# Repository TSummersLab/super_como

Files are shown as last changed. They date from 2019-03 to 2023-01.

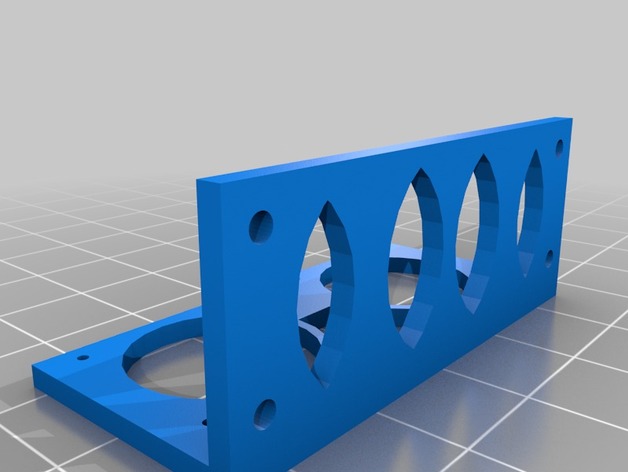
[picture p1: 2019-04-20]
CAD/ultrasonic_mount/images/f159fd88af9eb30a68ea307b06156ffa_preview_featured.jpg

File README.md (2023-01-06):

# Super COMO
Super COMO is an autonomous car platfrom at the University of Texas at Dallas. It is a hardware upgrade over the [COMO platform](https://github.com/TSummersLab/como).

Check out [our website](https://omarkabbas.github.io/supercomo/) for details about car assembly, build, and other guides and tutorials.

## Installation Guide

Before installing the Super COMO packages, perform a full JetPack installation on the Jetson TX2. For the package, JetPack 3.2.1 was installed. 

After installing JetPack, follow the steps below to setup Super COMO.

1. Configure repositories:
Configure repositories to allow "restricted," "universe," and "multiverse." Do this by following the instructions in [this link](https://help.ubuntu.com/community/Repositories/Ubuntu).

2. Clone super_como :
Clone the repository to your home directory. In a terminal window run:
```
cd ~ && git clone https://github.com/The-SS/super_como
```

3. Navigate to setup folder:
In terminal, navigate to the `setup` folder in `super_como` by running:
``` 
cd ~/super_como/setup
```

4. Configure git (if not configured):
Configure git either manually or by running `git_config_setup.sh`. You can run the setup file as follows:
```
./git_config_setup.sh
```

5. Run the following scripts:
```
./install_programs.sh

./install_ros.sh

```

6. Download and install the ZED SDK:
- Go to the [ZED downloads](https://www.stereolabs.com/developers/release/#sdkdownloads_anchor) website and download the [ZED SDK for Jetson TX2 with JetPack 3.2 and CUDA 9](https://download.stereolabs.com/zedsdk/2.7/tegrax2).

- Once it downloads, either used `chmod +x <file_name>` to make the file and executable or right click it --> permissions --> allow executing file as a program.

- Run the script by `cd` to file location in a terminal and typing `./` followed by the file name.

7. Setup the device rules:
Run the rules set up script:
```
sudo ./rules_setup.sh
```

This script will reload the rules, but we recommend restarting the machine to ensure that the rules are in effect.

8. Run the build script:
The `build.sh` script at the root of the super_como package builds the catkin workspace. In a terminal window, navigate to the root of the super_como package then run the following command:
```
cd ~/super_como
./build.sh
```

9. Generate the `ros_lib` libraries for arduino:
- Go the the Arduino `libraries` direcotry: 
```
cd ~/arduino-1.8.7/libraries
``` 
- Remove any previous `ros_lib` directory:
```
rm -fr ros_lib
```
- Generate the new libraries:
```
rosrun rosserial_arduino make_libraries.py .
```

For more details see the Install ros_lib into the Arduino Environment section [here](http://wiki.ros.org/rosserial_arduino/Tutorials/Arduino%20IDE%20Setup).

10. Source the workspace:
Every time a new terminal window is open you have to source your workspace.
```
source ~/super_como/workspace/devel/setup.bash
```
Alternatively, you can add the above to your bashrc file to avoid having to run it every time. To do that, run the following in a terminal.
```
echo "source ~/super_como/workspace/devel/setup.bash" >> ~/.bashrc
```
Once this runs you have to restart your terminal or source the bashrc file as follows:
```
source ~/.bashrc
```

11. Add the Lidar to ethernet networks:
- Open `Network Connections`.
- Click on `Add`.
- In the new window do the following:
	- Change the connection name to `lidar`
	- In the `General` tab, check the `Automatically connect to this network when it is available` and `All users may connect to this network` options
	- In the `IPv4 Settings` tab, change the `method` to `Manual` and add the following in `Addresses`:
		- address: 192.168.0.15
		- netmask: 255.255.255.0 (this will change to 24)
		- leave the `gateway` field empty
	- Click save.

12. Edit the USB port names:
The rules file generated by `rules_setup.sh` creates symbolic links for devices that should be used instead of the port names generated by Linux. The full list of symbolic links found in `/etc/udev/rules/99-device-rules.rules` is:
- `/dev/imu`: IMU
- `/dev/vesc`: VESC 
- `/dev/teensy`: Teensy
- `/dev/gps`: GPS module
- `/dev/elp/back`: back elp camera
- `/dev/elp/right`: righ elp camera
- `/dev/elp/left`: left elp camera
- `/dev/elp/front`: front elp camera

These links should be used in the package (instead of `/dev/ttyUSB*`, `/dev/ttyACM*`, or `/dev/video*`). Make the following modifications to the package:
- In `~/super_como/super_como/workspace/src/racecar/racecar/config/racecar-v2/vesc.yaml` change the `port` parameter under `vesc_driver` to `/dev/vesc`.
- In `~/super_como/workspace/src/razor_imu_9dof/config/razor.yaml` change the `port` parameter to `/dev/imu`.
- In `~/super_como/workspace/src/razor_imu_9dof/nodes/imu_node.py` change the `default_port` variable to `'/dev/imu'` (line 110). The updated line should be: `default_port='/dev/imu'`.

13. If running YOLO, change the `darknet_ros` camera topic: 
In `~/super_como/workspace/src/darknet_ros/darknet_ros/config/ros.yaml` change the `topic` parameter under `camera_reading` in `subscribers` to the desired image topic. For example that could be the `/zed/left/image_raw_color` topic if using the ZED or ZED mini cameras. Check the [YOLO github repository](https://github.com/leggedrobotics/darknet_ros/tree/7bc7ec0517b7107712da998f975584c88ed15f77) for more details.

## Operating the Package
Operating the package is a two step process:
1. Starting the sensors and hardware
2. Starting an autonomous feature
This decoupling allows for easy switching between autonomous features wihtout having to restart all sensor operation

#### To Start the Sensors and Hardware
1. Open `super_como/workspace/src/hardware_interface/launch/super_como.launch` and edit the `On/Off Switches` section (and save the changes). 
	- Setting the default value to `true` will start the component
	- Setting the default value to `false` will skip starting the component
2. Run the following in a terminal window:
```
roslaunch hardware_interface super_como.launch
```

The super_como.launch provides an all-in-one solution to starting all hardware components. Nonetheless, individual scripts can be launched. Any of the scripts in `super_como/workspace/src/hardware_interface/launch` or any of the other packages in workspace can be run individually to control a single (or multiple) device(s).

#### To Start an Autonomous Feature
1. Determine what application to run and edit the `super_como.launch` script to enable all the required sensors.
2. Run the appropriate launch file from `super_como/workspace/src/control/launch` to perform the desired feature by running the following in a terminal window: 
```
roslaunch control <file_name> 
```
Here, <file_name> is the desired launch file name.

Some of the autonomous features include the following:
- `hallway_navigation.launch`: requires the Hokuyo UST-10LX lidar
- `hallway_nav_wth_object_detection.launch`: requires the Hokuyo UST-10LX lidar and the camera used by `darknet_ros` (yolo) (ZED camear by default)
- `line_follower.launch`: requires the ZED camera
- `line_follower_with_lidar.launch`: requires the Hokuyo UST-10LX lidar and the ZED camera
- `darknet_ros.launch`: requires the camera used by `darknet_ros` (yolo) (ZED camear by default)

Other autonomous driving features can be designed similar to the first four included feature

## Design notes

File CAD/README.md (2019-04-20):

# CAD Files
CAD files for the Super COMO car.

# Description
- decks: 
	- Contains SolidWorks files (SLDPRT) for the decks and engineering drawings (PDF)
	- Machine the parts as follows:
		- Deck 1, Deck 2: Plastic
		- Deck 3: Aluminum
- elp_pole_mount:
	- Contains the stl files for the elp camera pole mount design (base and holder)
	- The original designer of these parts is Cheng Hao Yuan (chengyuan@berkeley.edu) and the parts are part of the [UCB BARC project](http://www.barc-project.com/) and can also be found [here](https://github.com/MPC-Berkeley/barc/tree/master/CAD/camera%20fixture)
	- 3D print the desired number using any material (ABS is fine)
- elp_seat_mount:
	- Contains the stl file for the elp camera seat mount design
	- The original designer of this part is Kevin Daniel (kmd140630@utdallas.edu)
	- 3D print the desired number using any material (ABS is fine)
- encoder_mount:
	- Contains the stl file and SolidWorks file (SLDPRT) for the encoder mount
 	- 3D print using any material (ABS is fine)
- encoder_disk:
	- Contains the stl file and SolidWorks file (SLDPRT) for the encoder disk
 	- 3D print using any material (ABS is fine)
- ultrasonic_mount:
	- Contains the stl file for the ultrasonic sensor mount (files/Ultraschallsensorhalterung_4.stl)
	- The original design is part of the Thingiverse database
	- 3D print using any material (ABS is fine)
- teensy_ckt:
	- Contains the Eagle board (BRD) and schematic (SCH) file, Gerber files, and PDFs
 for the teensy ckt
	- The schematic can be used to assemble the circuit. The Gerber files can be used to order the PCB.

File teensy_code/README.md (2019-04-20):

# Teensy Code

Contains the Teensy code to be flashed on the Teensy 3.5.

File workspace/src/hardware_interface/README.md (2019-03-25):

# SuperCOMO Hardware Interface

### Package Overview

This package is design to provide the necessary interface with the car's hardware. This includes initializing and starting the following devices:
- ZED camera
- Razor 9DoF IMU
- Hokuyo ust-10LX LIDAR
- VESC 

When this package establishes a communication with the hardware, it also provides ROS topics for other packages to publish/subscribe to the sensor/control hardware. These topics are documented below.

### Package Nodes

### Pakcage Topics

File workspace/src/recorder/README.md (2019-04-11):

### Recording the Basic Data 

This program record the basic out put of the main components including, Zed left and right images, LIDAR, IMU, and Teensy. It was created to reduce the data recorded as recording every message creates a huge file. 
#### Running Recorder

To run the program us rosrun to run the .cpp file in a terminal.
```
rosrun recorder recorder
```
This command will launch the file and start recording.

#### Recorded Topics

THis code record the following topics
 * scan                          : Message holding the raw LIDAR data
 * /zed/right/image_raw_color    : Message holding right ZED image
 * /zed/left/image_raw_color     : Message holding left ZED image
 * ultrasonics                   : Message holding the data from the ultrasonics
 * imu                           : Message holding the IMU data

#### Recording other Topics

You can record other topics using ros bag files to do so run the following command. 
```
rosbag record topic_name -O name.bag
```
This will create a bag named name and save topic_name to it. You can add a path to the bagfile name. /home/data/name.bag. you can also add more topics to be recorded.
```
rosbag record topic1 topic2 topic3 -O /home/data/name.bag
```

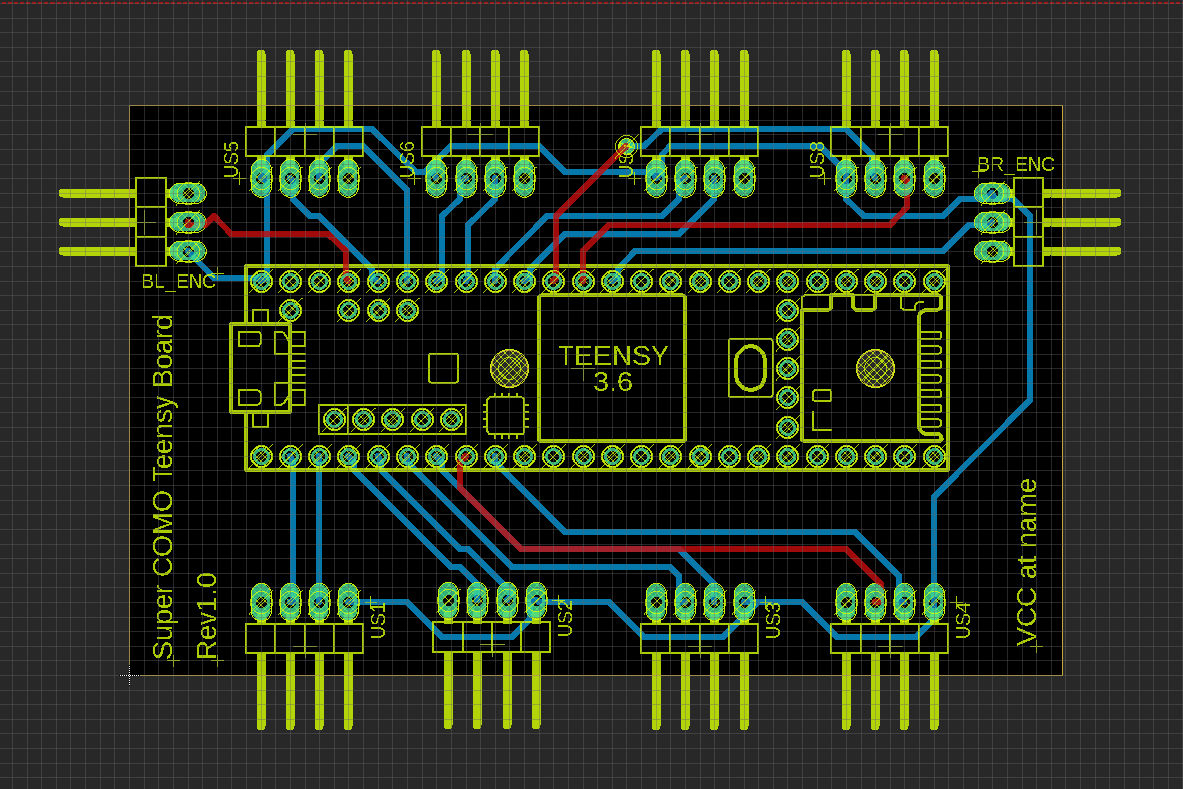
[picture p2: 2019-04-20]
CAD/teensy_ckt/Teensy_ckt.PNG

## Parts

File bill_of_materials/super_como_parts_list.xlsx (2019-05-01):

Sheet: Sheet1
Part Name | Vendor | Vendor Part Number | Quantity | Unit cost | Cost per quantity | Amount Used | Cost Per Amount used | Notes | Link | Alternatives
3D printed parts, machining, and PCb not included
Costs exclude discounts (other than quantity discounts),
shipping costs, or bundle discounts (or options)
Part Name | Vendor | Vendor Part Number | Quantity | Unit cost | Cost per quantity | Amount Used | Cost Per Amount used | Notes | Link | Alternatives
Chassis and Accessories
Traxxas Slash 4x4 Platinum | Traxxas | 6804R | 1 | 429.99 | 429.99 | 1 | 429.99 |  | https://traxxas.com/products/models/electric/6804Rslash4x4platinum?t=overview
Tall battery hold-down and retainer set | Traxxas | 7426X | 1 | 6.5 | 6.5 | 1 | 6.5 |  | https://traxxas.com/products/parts/7426X
RACECAR/J Spring upgrade set | RACECAR/J | N/A | 1 | 29.5 | 29.5 | 1 | 29.5 |  | https://racecarj.com/collections/parts/products/spring-upgrade
Decks and Mounts
0.25" x 24" x 48" Black ABS plastic sheet | ePlastics | ABSBLK0.250HC24X48 | 1 | 33.83 | 33.83 | 0.5 | 16.915 |  | https://www.eplastics.com/ABSBLK0-250HC24X48
0.08" x 12" x 12" 6061-T6 Aluminum sheet | OnlineMetals |  | 1 | 12.69 | 12.69 | 0.12 | 1.5228 |  | https://www.onlinemetals.com/en/buy/aluminum/aluminum-sheet-6061-t6/pid/1243
Magnus Folding Z-Head | B&H | MAZH3 | 1 | 24.95 | 24.95 | 1 | 24.95 |  | https://www.bhphotovideo.com/c/product/1399721-REG/magnus_zh_3_z_tripod_head_with.html
Sensors
Hokuyo UST-10LX laser range finder | RobotShop | Rob-Hok-24 | 1 | 1600 | 1600 | 1 | 1600 |  | https://www.robotshop.com/en/hokuyo-ust-10lx-scanning-laser-rangefinder.html
ZED stereo camera | StereoLabs | N/A | 1 | 449 | 449 | 1 | 449 |  | https://store.stereolabs.com/products/zed/?_ga=2.24819577.297723185.1555287229-1218582592.1555287229
ELP 1080p camera | Amazon | N/A | 4 | 45.99 | 183.96 | 4 | 183.96 |  | https://www.amazon.com/ELP-Camera-Megapixel-Windows-Android/dp/B00KA7WSSU
HC-SR04 ultrasonic sensors | Sparkfun | SEN-13959 | 8 | 3.95 | 31.6 | 8 | 31.6 |  | https://www.sparkfun.com/products/13959 | https://www.amazon.com/Ultrasonic-LGDehome-Measuring-Distance-Transmitter/dp/B07558LH2P?s=gateway
Sparkfun digital breakout light breakout | Sparkfun | ROB-09454 | 2 | 2.95 | 5.9 | 2 | 5.9 |  | https://www.sparkfun.com/products/9454
Razor 9DoF IMU | Sparkfun | SEN-14001 | 1 | 35.95 | 35.95 | 1 | 35.95 |  | https://www.sparkfun.com/products/14001
VK-162 G-Mouse GPS USB dongle | Amazon | N/A | 1 | 15.99 | 15.99 | 1 | 15.99 |  | https://www.amazon.com/Navigation-External-Receiver-Raspberry-Geekstory/dp/B078Y52FGQ?s=gateway
Computers and Microcontrollers
Teensy 3.5 | Sparkfun | DEV-14055 | 1 | 24.95 | 24.95 | 1 | 24.95 |  | https://www.sparkfun.com/products/14055
Jetson TX2 development kit | Arrow | N/A | 1 | 599 | 599 | 1 | 599 |  | https://www.arrow.com/en/products/945-82771-0000-000/nvidia
VESC 11.0 electronic speed controller | RobotShop | RB-May-76 | 1 | 89.9 | 89.9 | 1 | 89.9 |  | https://www.robotshop.com/en/maytech-vesc-50a-brushless-speed-controller-eskateboard-robotics.html
Other Electronics
7-port powered USB hub | B&H | TPUH700 | 1 | 29.99 | 29.99 | 1 | 29.99 |  | https://www.bhphotovideo.com/c/product/1141563-REG/tp_link_uh700_usb_3_0_7_port.html | https://www.amazon.com/AmazonBasics-Port-USB-Power-Adapter/dp/B00E6GX4BG?s=electronics
Startech 4 port PCI express usb 3.0 card with 4 dedicarted 5Gbps Channels and UASP - SATA/LP4 power (PEXUSB3S44V) | CDW | 3255376 | 1 | 58.99 | 58.99 | 1 | 58.99 |  | https://www.cdw.com/product/startech.com-4-port-pci-express-usb-3.0-card-w-4-dedicated-channels-uasp/3255376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
Samsung 500GB 860 Evo SATA III 2.5" SSD | B&H | SAMZ76E500BA | 1 | 81.99 | 81.99 | 1 | 81.99 |  | https://www.bhphotovideo.com/c/product/1382498-REG/samsung_mz_76e500b_am_860_evo_500gb_internal.html
Power Sources
Traxxas 8,400mAh 11.1V 3-cell LiPo | Traxxas | 2878X | 1 | 155.99 | 155.99 | 1 | 155.99 |  | https://traxxas.com/products/parts/batteries/idpowercellbatteries/lipo/2878X-8400mah-111v-3S-25C
Traxxas LiPo battery charger | Traxxas | 2970 | 1 | 49.99 | 49.99 | 0 | 0 |  | https://traxxas.com/products/parts/chargers/2970ezpeakplus4ampid
XTPower XT-20000QC2 powerbank | Amazon | N/A | 1 | 79.9 | 79.9 | 1 | 79.9 |  | https://www.amazon.com/XTPower-MP-10000-External-10000mAh-included/dp/B06XWTY96G?th=1
Screws, Nuts, Spacers, and Standoffs
0.25"-20x0.5" screws | Fastenal | 10800 | 1 | 0.1723 | 0.1723 | 1 | 0.1723 |  | https://www.fastenal.com/product/fasteners/bolts/hex-cap-screws-and-hex-bolts/600003?categoryId=600003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"&Dia/Thread Size=1/4"-20&productFamilyId=25570
M0-80x0.25” screws | Fastenal | 170300 | 16 | 0.1002 | 1.6032 | 16 | 1.6032 |  | https://www.fastenal.com/product;jsessionid=XA9A4YiOjwef9Yjc8+nbU2H1.38536438-9c19-3947-9017-bf77ad0514fd?query=0170300&fsi=1
M2-0.4x10mm screws | Fastenal | 173298 | 16 | 0.0516 | 0.8256 | 16 | 0.8256 |  | https://www.fastenal.com/products/details/0173298?isPunchout=false
M2.5-0.45x8mm screws | Fastenal | QM2490008A20000 | 6 | 0.0754 | 0.4524 | 6 | 0.4524 |  | https://www.fastenal.com/product?query=QM2490008A20000&fsi=1
M2.5-0.45x10mm screws | Fastenal | QM2490010A20000 | 9 | 0.0781 | 0.7029 | 9 | 0.7029 |  | https://www.fastenal.com/product?query=QM2490010A20000&fsi=1
M3x6mm plastic screws | Digi-Key | 732-13702-ND | 4 | 0.26 | 1.04 | 4 | 1.04 | * | https://www.digikey.com/product-detail/en/wurth-electronics-inc/97790403111/732-13702-ND/10056385
M3-0.5x8mm screws | Fastenal | QM2510008A20000 | 6 | 0.0321 | 0.1926 | 6 | 0.1926 |  | https://www.fastenal.com/product?query=QM2510008A20000&fsi=1
M3-0.5x10mm screws | Fastenal | QM2510010A20000 | 6 | 0.0511 | 0.3066 | 6 | 0.3066 |  | https://www.fastenal.com/products/details/QM2510010A20000?isPunchout=false
M3-0.5x12mm screws | Fastenal | QM2510012A20000 | 20 | 0.0552 | 1.104 | 20 | 1.104 |  | https://www.fastenal.com/products/details/QM2510012A20000?isPunchout=false
M3-0.5x20mm screws | Fastenal | QM2510020A20000 | 4 | 0.0691 | 0.2764 | 4 | 0.2764 |  | https://www.fastenal.com/product?query=QM2510020A20000&fsi=1
M0-80 nuts | Fastenal | 70701 | 16 | 0.2221 | 3.5536 | 16 | 3.5536 |  | https://www.fastenal.com/product?query=70701&fsi=1
M2-0.4 nuts | Fastenal | MN2460000A20000 | 16 | 0.0843 | 1.3488 | 16 | 1.3488 |  | https://www.fastenal.com/product?query=MN2460000A20000&fsi=1
M2.5-0.45 nuts | Fastenal | MN2490000A20000 | 6 | 0.0559 | 0.3354 | 6 | 0.3354 |  | https://www.fastenal.com/product?query=MN2490000A20000 &fsi=1
M3-0.5 nuts | Fastenal | MN2510000A40000 | 20 | 0.034 | 0.68 | 20 | 0.68 | ** | https://www.fastenal.com/products/details/MN2510000A40000?isPunchout=false
M3-0.5 plastic nut | Digi-Key | 732-12637-ND | 2 | 0.1 | 0.2 | 2 | 0.2 | * | https://www.digikey.com/product-detail/en/wurth-electronics-inc/709940300/732-12637-ND/9488341
M3x10mm plastic spacers | Digi-Key | 732-12994-ND | 2 | 0.85 | 1.7 | 2 | 1.7 | * | https://www.digikey.com/product-detail/en/wurth-electronics-inc/970100365/732-12994-ND/9488698
M3x10mm spacers | Digi-Key | 732-12847-ND | 2 | 0.46 | 0.92 | 2 | 0.92 | ** | https://www.digikey.com/product-detail/en/wurth-electronics-inc/970100354/732-12847-ND/9488551
M3x10mm standoffs | Digi-Key | 36-24337-ND | 6 | 0.45 | 2.7 | 6 | 2.7 | ** | https://www.digikey.com/product-detail/en/keystone-electronics/24337/36-24337-ND/1532138
M3x20mm standoffs | Digi-Key | 36-24341-ND | 2 | 0.73 | 1.46 | 2 | 1.46 | ** | https://www.digikey.com/product-detail/en/keystone-electronics/24341/36-24341-ND/1532142
M3x 50mm standoffs (combine two to make M3x100mm standoffs) | Digi-Key | 732-12979-ND | 10 | 2.34 | 23.4 | 10 | 23.4 | *** | https://www.digikey.com/product-detail/en/wurth-electronics-inc/971500324/732-12979-ND/9488683
Vibration damper standoffs 4pc pack | Amazon | N/A | 1 | 9.49 | 9.49 | 1 | 9.49 |  | https://www.amazon.com/Flight-Controller-Vibration-Damper-Damping/dp/B07L1N6WDK?s=gateway | can be replaced by 10mm plastic/nylon standoffs
Header Pins and Cables
24-pin male headers | Digi-key | 732-5331-ND | 2 | 1.23 | 2.46 | 2 | 2.46 | **** | https://www.digikey.com/product-detail/en/wurth-electronics-inc/61302411121/732-5331-ND/4846867
24-pin female headers | Amazon | N/A | 1 | 5.6 | 5.6 | 0.2 | 1.12 | **** | https://www.amazon.com/Haobase-2-54mm-Straight-Single-Headers/dp/B01DLX6RSQ?s=industrial
4-pin male headers | Digi-key | 732-5317-ND | 8 | 0.18 | 1.44 | 8 | 1.44 |  | https://www.digikey.com/product-detail/en/wurth-electronics-inc/61300411121/732-5317-ND/4846827
3-pin male headers | Digi-key | 732-5316-ND | 2 | 0.13 | 0.26 | 2 | 0.26 |  | https://www.digikey.com/product-detail/en/wurth-electronics-inc/61300311121/732-5316-ND/4846825
12" 4-wire female-to-female connectors | Digi-key | 1568-1936-ND | 8 | 1.95 | 15.6 | 8 | 15.6 |  | https://www.digikey.com/product-detail/en/sparkfun-electronics/PRT-10374/1568-1936-ND/9657952
300mm 3-wire male-to-female servo connectors | Digi-key | 1738-1331-ND | 2 | 0.77 | 1.54 | 2 | 1.54 |  | https://www.digikey.com/product-detail/en/dfrobot/FIT0033/1738-1331-ND/7597074
SATA with power extension cable | CDW | 2957912 | 1 | 9.99 | 9.99 | 1 | 9.99 |  | https://www.cdw.com/product/C2G-22-Pin-SATA-Extension-Cable-SATA-extension-cable-1-ft/2957912?pfm=srh
PCIe X4 extension cable | Amazon | N/A | 1 | 8.99 | 8.99 | 1 | 8.99 |  | https://www.amazon.com/TENEXT-Express-Flexible-Extension-Ribbon/dp/B06WWNVKT2
1 Female - 3 Male barrel plug splitter (2.5mm ID x 5.5mm OD) | Digi-key | 839-1467-ND | 1 | 6.08 | 6.08 | 1 | 6.08 |  | https://www.digikey.com/product-detail/en/tensility-international-corp/10-02726/839-1467-ND/8753157
1 Female - exposed wire barrel plug (2.5mm ID x 5.5mm OD) | Digi-key | 839-1461-ND | 1 | 3.18 | 3.18 | 1 | 3.18 |  | https://www.digikey.com/product-detail/en/tensility-international-corp/10-02960/839-1461-ND/8660983
1 Male - exposed wire barrel plug (2.5mm ID x 5.5mm OD) | Digi-key | CP-2186-ND | 1 | 3.84 | 3.84 | 1 | 3.84 |  | https://www.digikey.com/product-detail/en/tensility-international-corp/CA-2186/CP-2186-ND/568577 | can also be cut from the USB hub barrel plug cable
12" Male USB A to Male Micro USB B cable | Digi-Key | TL1795-ND | 2 | 4.9 | 9.8 | 2 | 9.8 |  | https://www.digikey.com/product-detail/en/tripp-lite/UR050-001-24G/TL1795-ND/5359392
Misc
Liquid white-out | OfficeSupply | BICWOSQPP11 | 1 | 1.97 | 1.97 | 0.1 | 0.197 |  | https://www.officesupply.com/office-supplies/writing-correction/correction-supplies-erasers/correction-pens/wite-shake-squeeze-correctable/p26604.html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
Black permanent marker | Staples | 500850 | 1 | 1.44 | 1.44 | 0.1 | 0.144 |  | https://www.staples.com/Avery-Marks-A-Lot-Large-Permanent-Markers-Chisel-Tip-Black-Each/product_500850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
Velcro / 3M dual lock | iTapeStore | SJ3550_1 | 1 | 13.75 | 13.75 | 0.02 | 0.275 |  | https://www.itapestore.com/3m-dual-lock-sj3550-by-the-yard.html
Heat shrink | Amazon | N/A | 1 | 8.99 | 8.99 | 0.1 | 0.899 |  | https://www.amazon.com/560PCS-Heat-Shrink-Tubing-Eventronic/dp/B072PCQ2LW
thermal paste | Digi-Key | CW7270-ND | 1 | 14.02 | 14.02 | 0.2 | 2.804 |  | https://www.digikey.com/product-detail/en/chemtronics/CW7270/CW7270-ND/1929220
Gaming controller (Logitech F310 Gamepad) | B&H | LOF310 | 1 | 19.35 | 19.35 | 0 | 0 |  | https://www.bhphotovideo.com/c/product/758301-REG/Logitech_940000110_F310_Gamepad.html?sts=pi | https://www.bhphotovideo.com/c/product/1358897-REG/hyperkin_m04314_bk_xbox_360_microsoft_wireless.html
 |  |  |  |  | 4211.3238 |  | 4073.5706
* : can be replaced by M3 Nylon standoffs kit | Amazon | N/A | 1 | 8.9 | 8.9 | 0.25 | 2.225 |  | https://www.amazon.com/HOBBYMATE-Standoffs-Quadcopter-Building-Motherboard/dp/B01I0SORIE
**: can be replaced by M3 brass spacer standoff kit | Amazon | N/A | 1 | 10.99 | 10.99 | 0.5 | 5.495 |  | https://www.amazon.com/eBoot-Pieces-Female-Standoff-Assortment/dp/B07BRK411L
***: can be replaced by 20pc M3 50mm +6mm standoffs | Amazon | N/A | 1 | 8.41 | 8.41 | 0.5 | 4.205 |  | https://www.amazon.com/uxcell-Female-Thread-Standoff-Spacer/dp/B00AO4332O?s=hi
****: can be replaced by 30 pcs 40 pin headers | Amazon | N/A | 1 | 6.99 | 6.99 | 0.133 | 0.92967 |  | https://www.amazon.com/dp/B074HVBTZ4?p
 |  |  |  |  | 4206.4538 |  | 4050.74527

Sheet: Sheet2
Costs for machining and 3D printing
Estimates:
Decks | hours | cost per hour | Cost | 3D printing part | Count | Cost per unit | Cost
all 3 on waterjet | 1.5 | 82.54 | 123.81 | Ultrasonic mount | 8
 |  |  |  | encoder mount | 2
 |  |  |  | encoder disk | 2
 |  |  |  | seat mount | 1
 |  |  |  | pole mount | 3

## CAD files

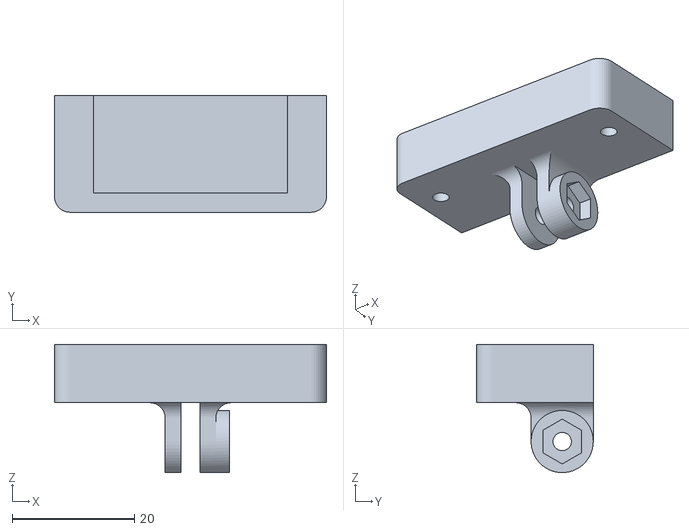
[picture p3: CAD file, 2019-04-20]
CAD/elp_pole_mount/elp_pole_mount_holder.stl
44.5 x 19.0 x 21.0

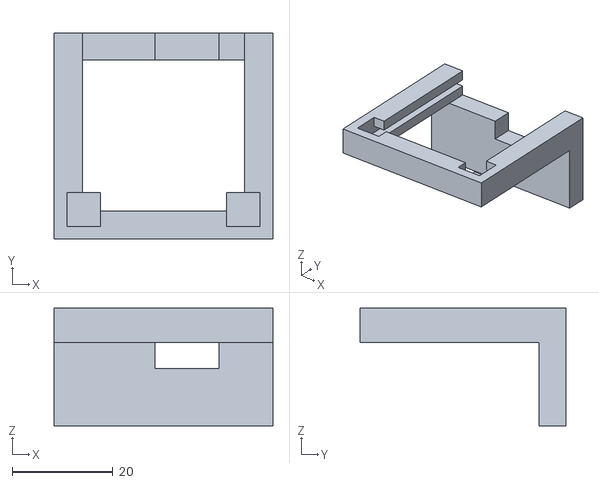
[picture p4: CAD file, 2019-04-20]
CAD/elp_seat_mount/elp_seat_mount.stl
43.4 x 40.9 x 23.4

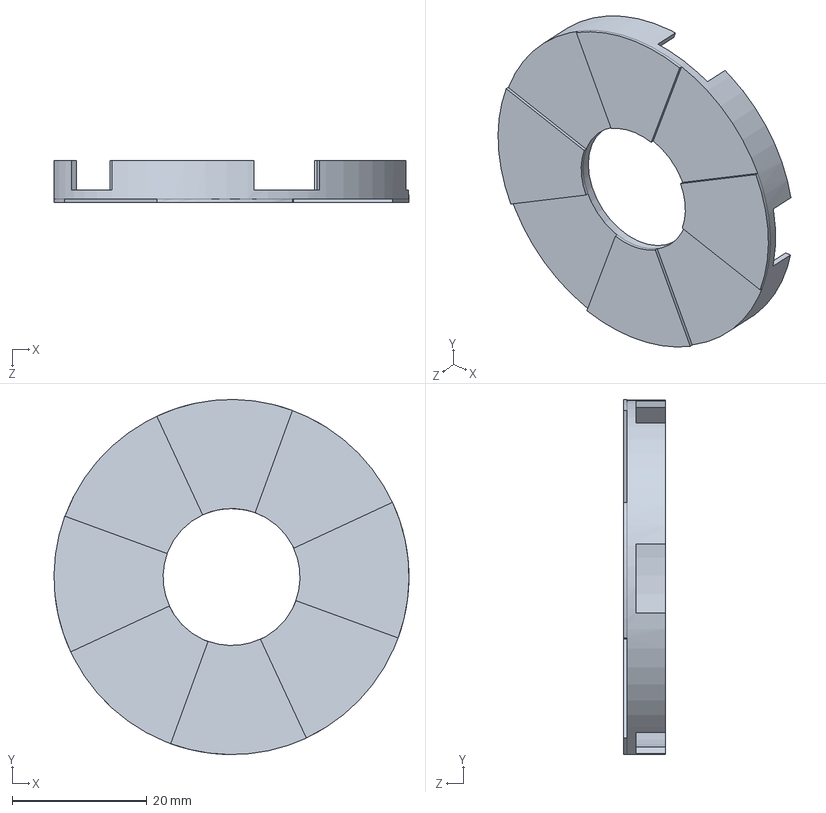
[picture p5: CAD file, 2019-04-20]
CAD/encoder_disk/encoder_disk.SLDPRT
52.7 x 52.8 x 6.24 mm

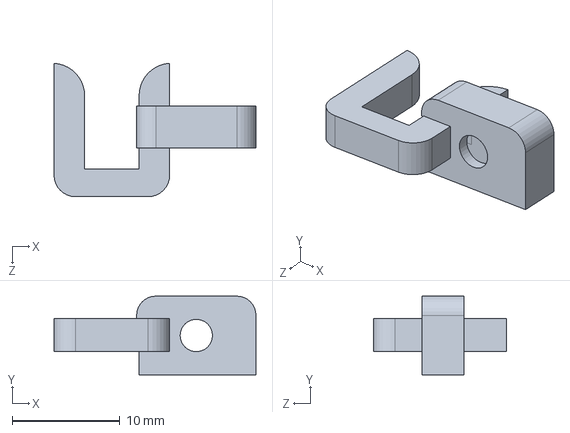
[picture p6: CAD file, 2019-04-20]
CAD/encoder_mount/encoder_mount.SLDPRT
18.7 x 7.30 x 12.4 mm

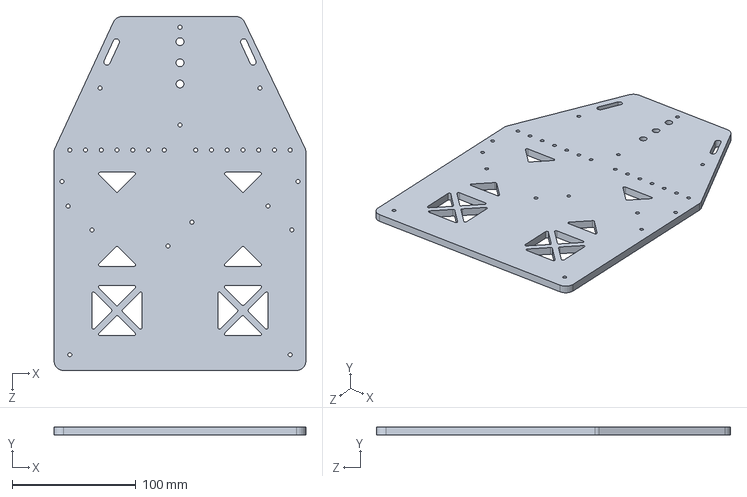
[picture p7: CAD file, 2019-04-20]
CAD/hammerhead_decks/deck2.SLDPRT
203.2 x 6.35 x 285.5 mm

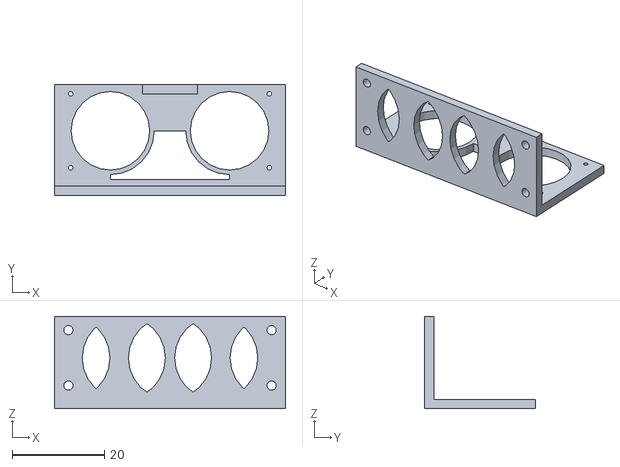
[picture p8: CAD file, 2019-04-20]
CAD/ultrasonic_mount/files/Ultraschallsensorhalterung_4.stl
50.0 x 24.0 x 20.0

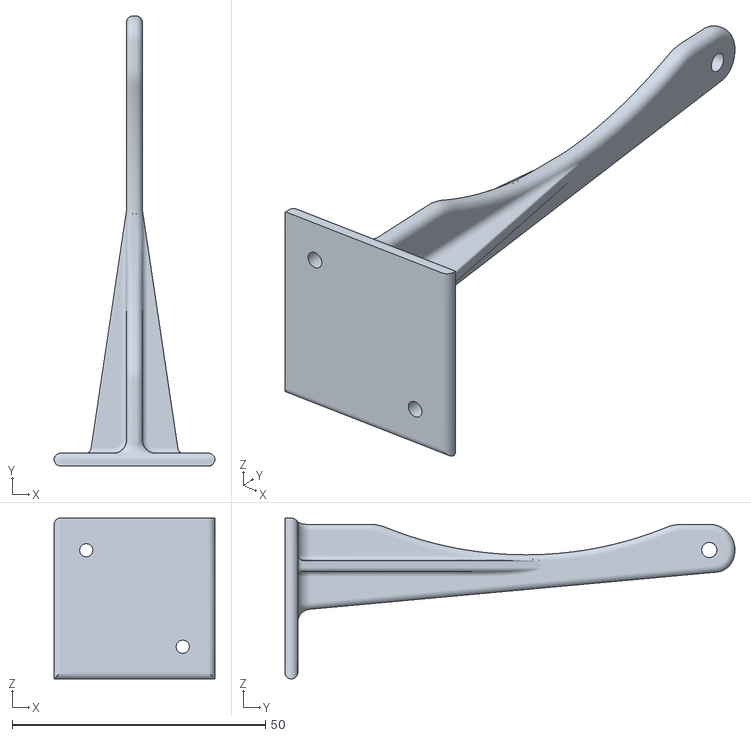
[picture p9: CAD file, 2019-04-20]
CAD/elp_pole_mount/elp_pole_mount_base.stl
31.8 x 88.8 x 31.8

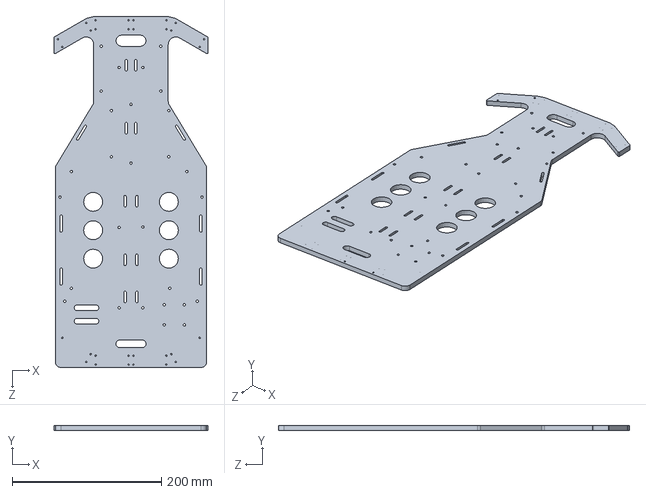
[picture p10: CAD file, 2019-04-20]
CAD/hammerhead_decks/deck1.SLDPRT
206.5 x 6.35 x 470.9 mm

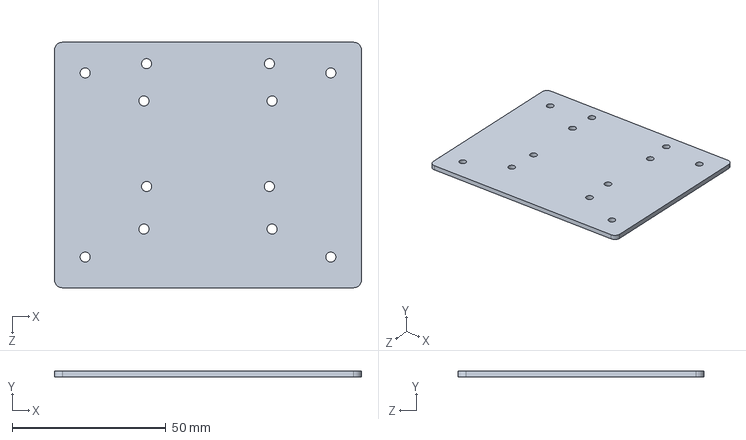
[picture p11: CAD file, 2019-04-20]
CAD/hammerhead_decks/deck3.SLDPRT
100.0 x 2.03 x 80.0 mm

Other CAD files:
CAD/encoder_disk/encoder_disk.STL
CAD/encoder_mount/encoder_mount.STL

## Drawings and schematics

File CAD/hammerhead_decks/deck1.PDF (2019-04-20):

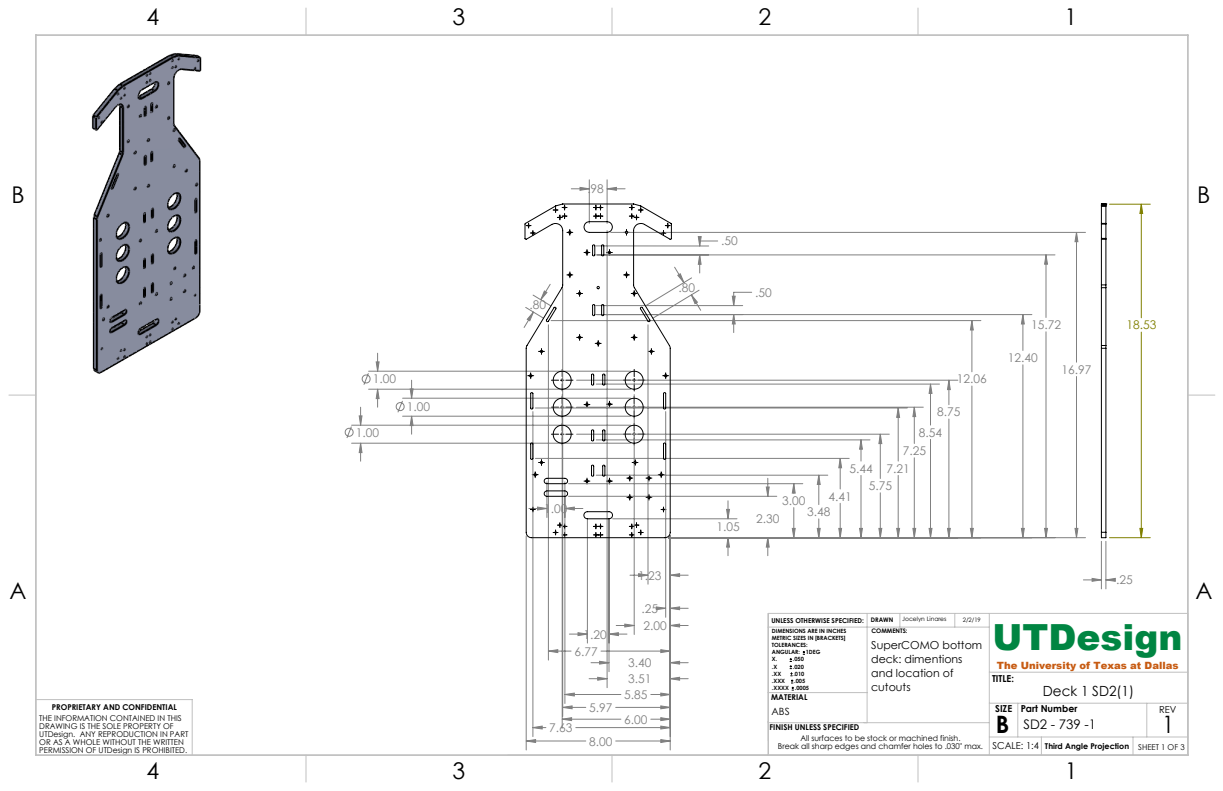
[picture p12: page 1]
Deck 1 SD2(1); SHEET 1 OF 3; SCALE: 1:4; PERMISSION OF UTDesign IS PROHIBITED.; Third Angle Projection; ABS; Part Number

UNLESS OTHERWISE SPECIFIED: | DRAWN | Jocelyn Linares | 2/2/19 | UTDesign The University of Texas at Dallas
DIMENSIONS ARE IN INCHES METRIC SIZES IN [BRACKETS] TOLERANCES: ANGULAR: 1DEG X. .050 .X .020 .XX .010 .XXX .005 .XXXX .0005 | COMMENTS: SuperCOMO bottom deck: dimentions and location of cutouts

MATERIAL
FINISH UNLESS SPECIFIED
All surfaces to be stock or machined finish.
Break all sharp edges and chamfer holes to .030" max.

PROPRIETARY AND CONFIDENTIAL
THE INFORMATION CONTAINED IN THIS
DRAWING IS THE SOLE PROPERTY OF
UTDesign. ANY REPRODUCTION IN PART
OR AS A WHOLE WITHOUT THE WRITTEN

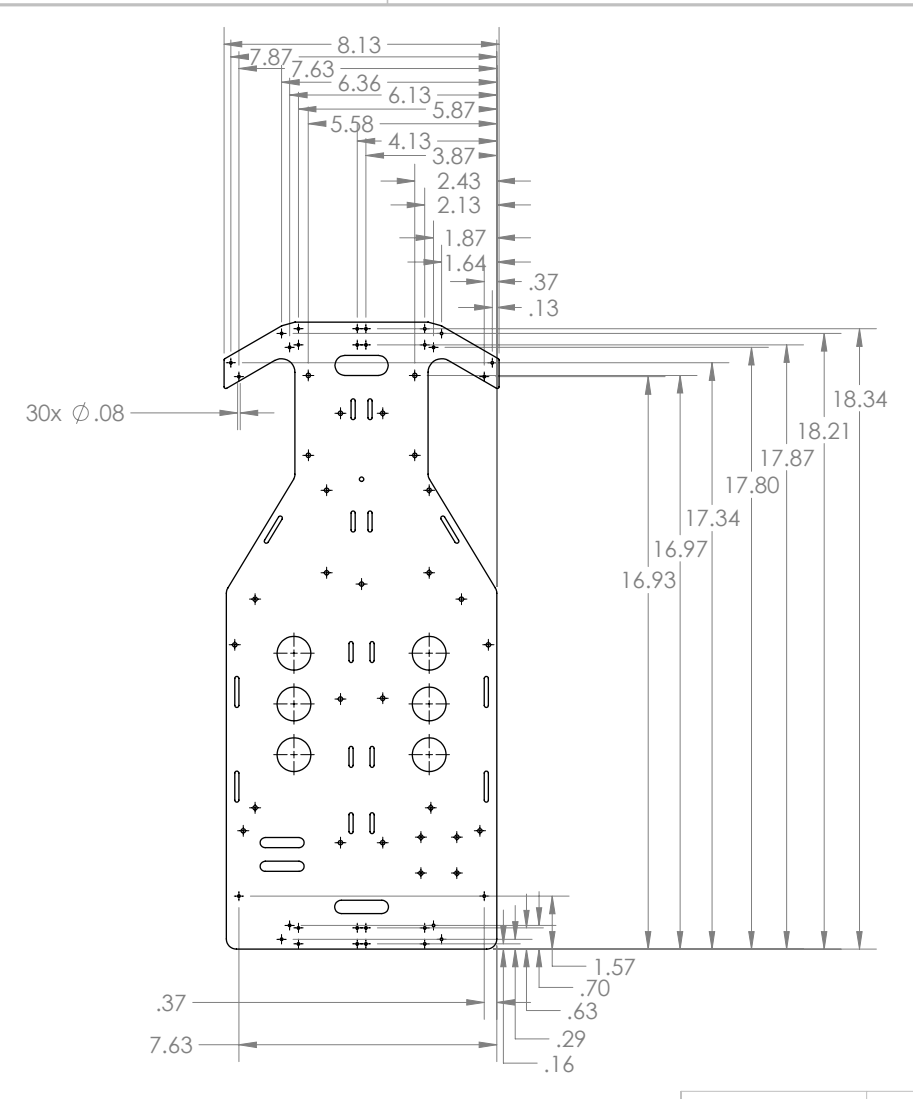
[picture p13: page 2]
Deck 1 SD2(1); ABS; Part Number

UNLESS OTHERWISE SPECIFIED: | DRAWN | Jocelyn Linares | 2/2/19 | UTDesign The University of Texas at Dallas
DIMENSIONS ARE IN INCHES METRIC SIZES IN [BRACKETS] TOLERANCES: ANGULAR: 1DEG X. .050 .X .020 .XX .010 .XXX .005 .XXXX .0005 | COMMENTS: SuperCOMO bottom deck: location of 0.08" holes

PROPRIETARY AND CONFIDENTIAL
THE INFORMATION CONTAINED IN THIS

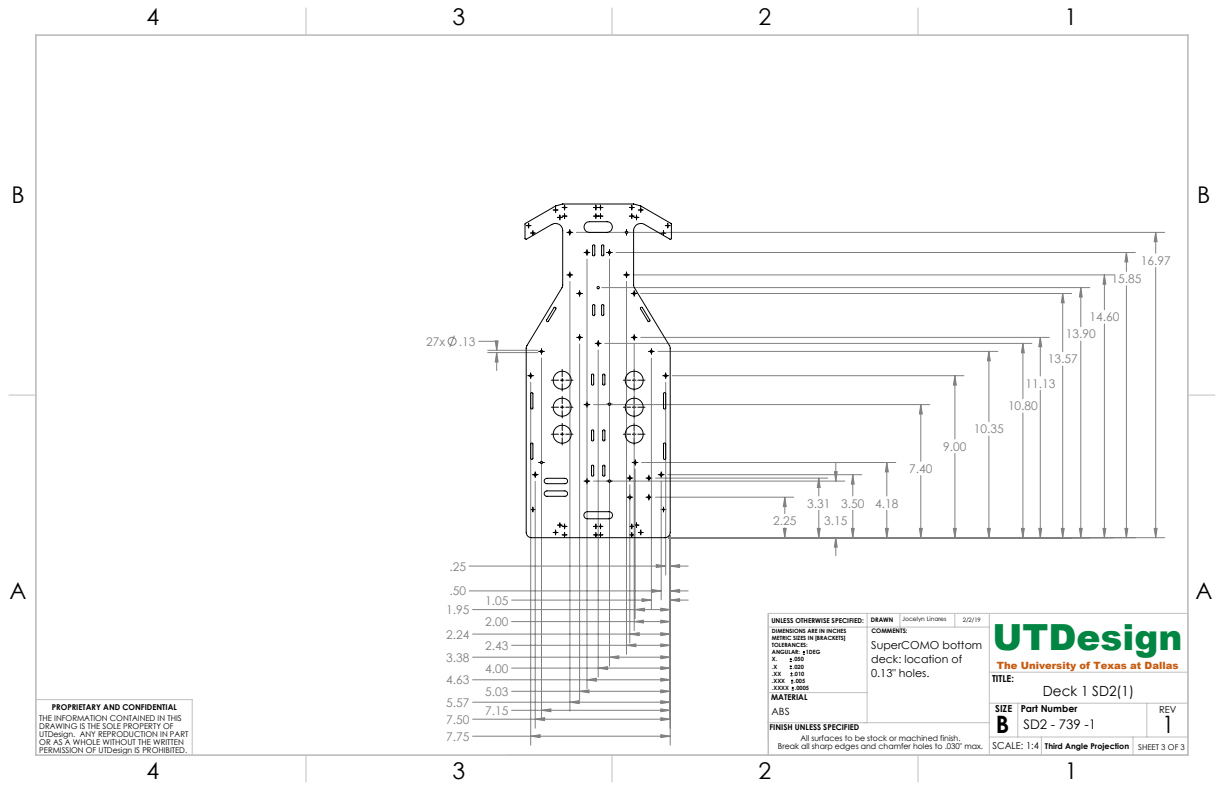
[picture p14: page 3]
Deck 1 SD2(1); ABS; Part Number

UNLESS OTHERWISE SPECIFIED: | DRAWN | Jocelyn Linares | 2/2/19 | UTDesign The University of Texas at Dallas
DIMENSIONS ARE IN INCHES METRIC SIZES IN [BRACKETS] TOLERANCES: ANGULAR: 1DEG X. .050 .X .020 .XX .010 .XXX .005 .XXXX .0005 | COMMENTS: SuperCOMO bottom deck: location of 0.13" holes.

PROPRIETARY AND CONFIDENTIAL
THE INFORMATION CONTAINED IN THIS

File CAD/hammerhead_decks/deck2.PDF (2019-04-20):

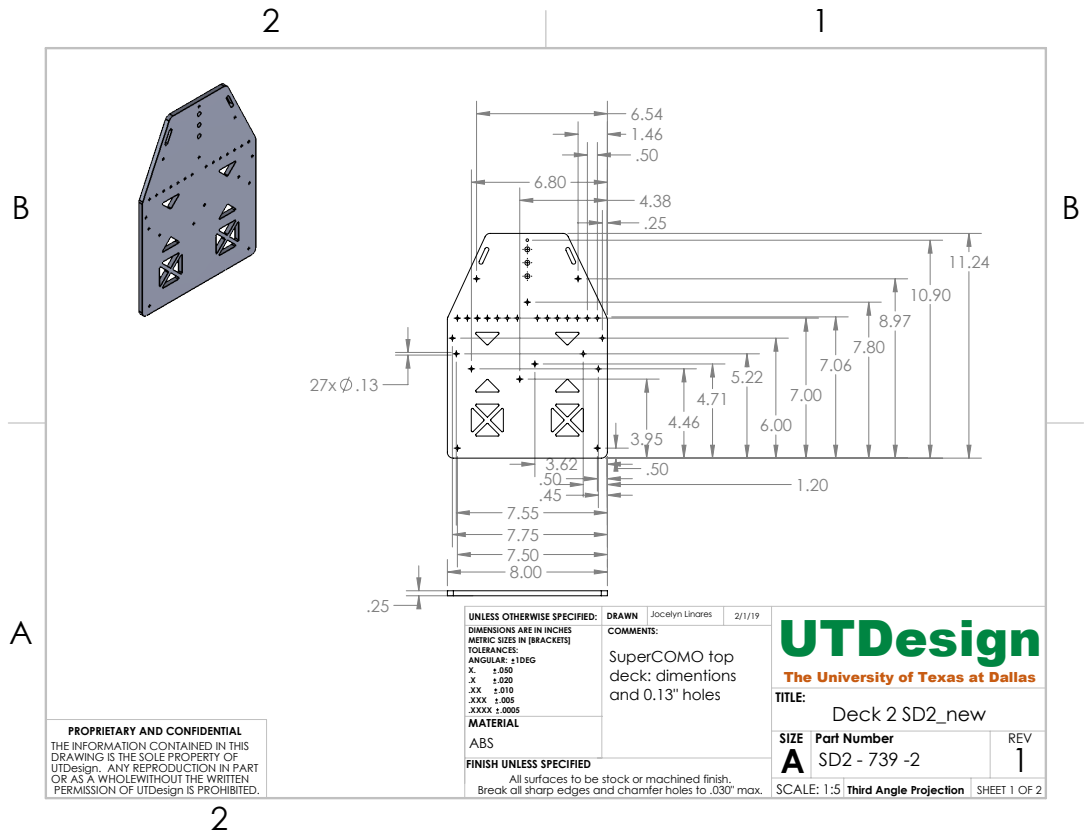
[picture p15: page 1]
ABS; Part Number; SCALE: 1:5; SHEET 1 OF 2; Deck 2 SD2_new

UNLESS OTHERWISE SPECIFIED: | DRAWN | Jocelyn Linares | 2/1/19 | UTDesign The University of Texas at Dallas
DIMENSIONS ARE IN INCHES METRIC SIZES IN [BRACKETS] TOLERANCES: ANGULAR: 1DEG X. .050 .X .020 .XX .010 .XXX .005 .XXXX .0005 | COMMENTS: SuperCOMO top deck: dimentions and 0.13" holes

MATERIAL
FINISH UNLESS SPECIFIED
All surfaces to be stock or machined finish.
Break all sharp edges and chamfer holes to .030" max.

PROPRIETARY AND CONFIDENTIAL
1 THE INFORMATION CONTAINED IN THIS
DRAWING IS THE SOLE PROPERTY OF
UTDesign. ANY REPRODUCTION IN PART
OR AS A WHOLEWITHOUT THE WRITTEN
PERMISSION OF UTDesign IS PROHIBITED.

Third Angle Projection

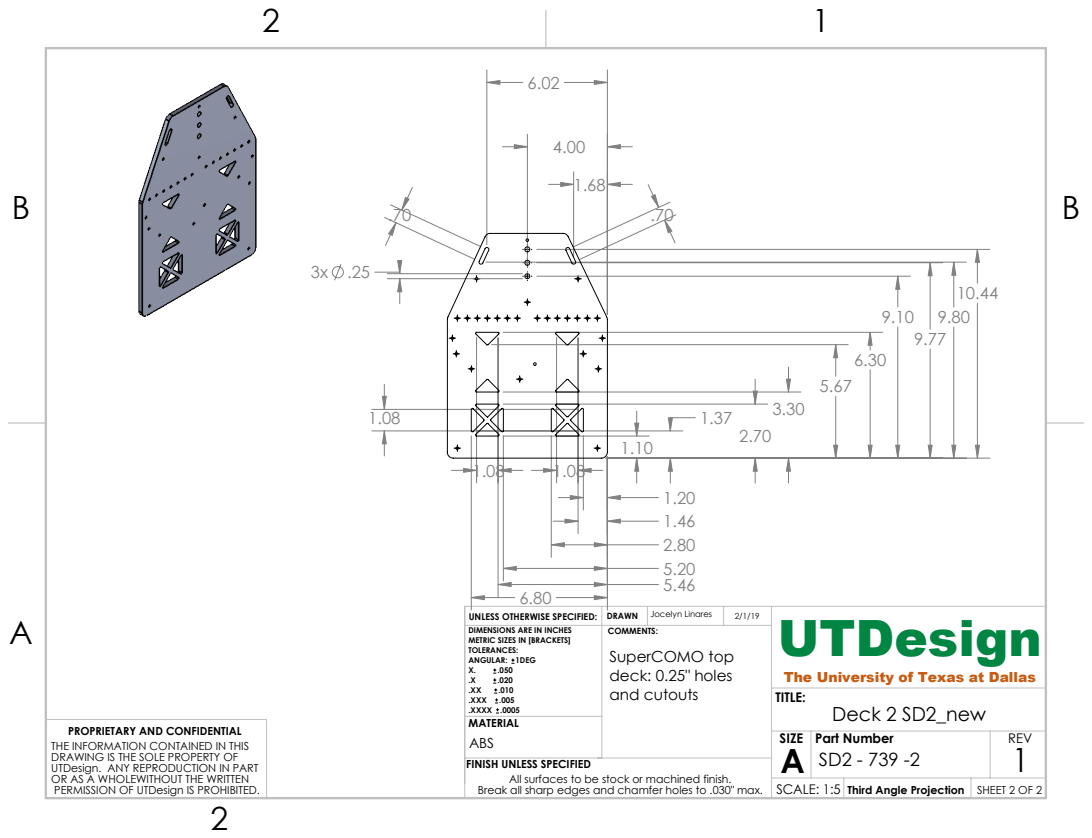
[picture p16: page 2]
ABS; Part Number; SCALE: 1:5; SHEET 2 OF 2; Deck 2 SD2_new

UNLESS OTHERWISE SPECIFIED: | DRAWN | Jocelyn Linares | 2/1/19 | UTDesign The University of Texas at Dallas
DIMENSIONS ARE IN INCHES METRIC SIZES IN [BRACKETS] TOLERANCES: ANGULAR: 1DEG X. .050 .X .020 .XX .010 .XXX .005 .XXXX .0005 | COMMENTS: SuperCOMO top deck: 0.25" holes and cutouts

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

Third Angle Projection

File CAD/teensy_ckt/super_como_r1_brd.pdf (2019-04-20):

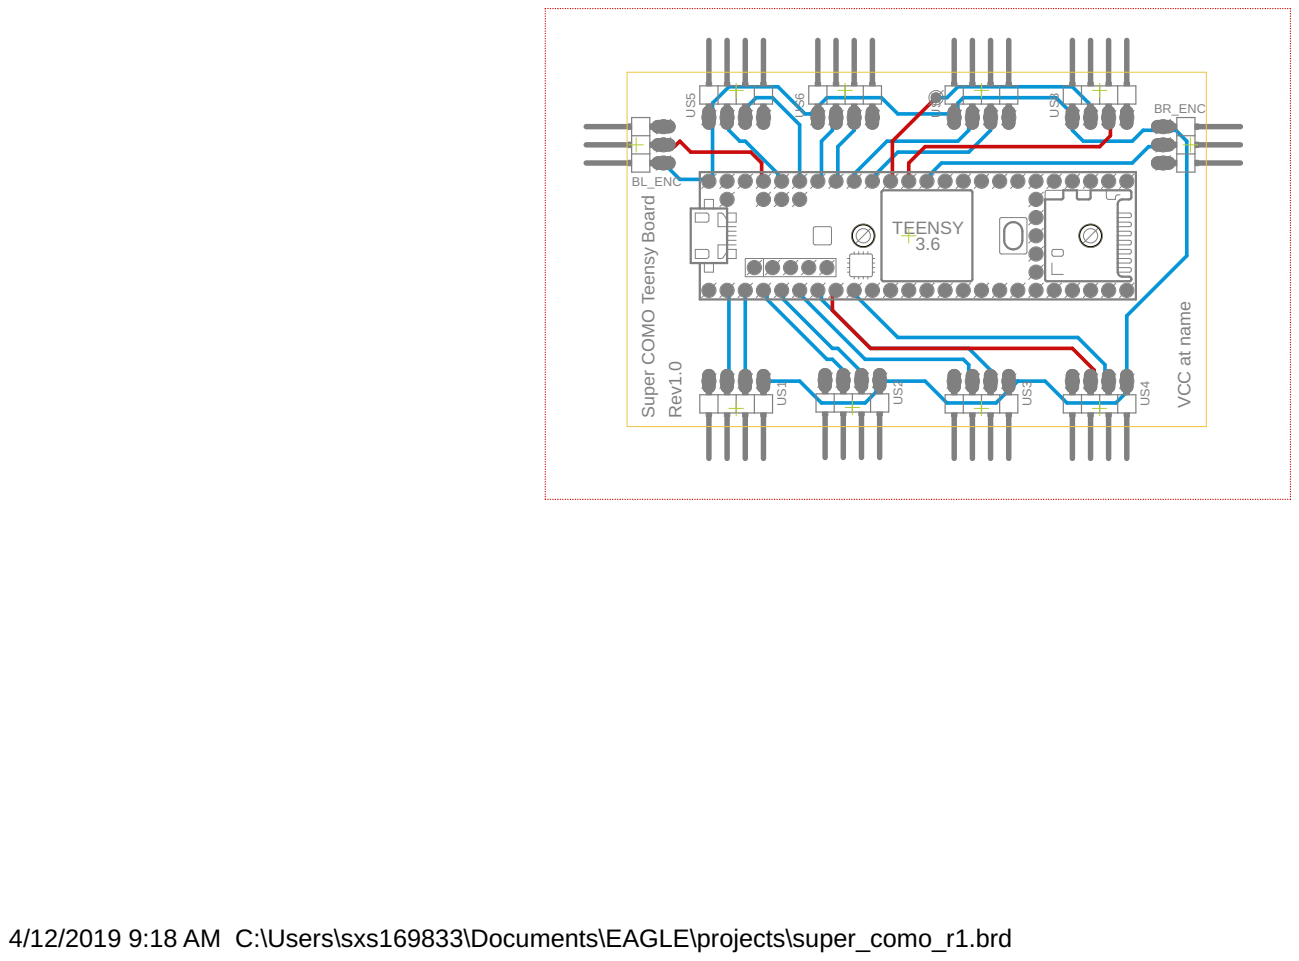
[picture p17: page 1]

4/12/2019 9:18 AM C:\Users\sxs169833\Documents\EAGLE\projects\super_como_r1.brd

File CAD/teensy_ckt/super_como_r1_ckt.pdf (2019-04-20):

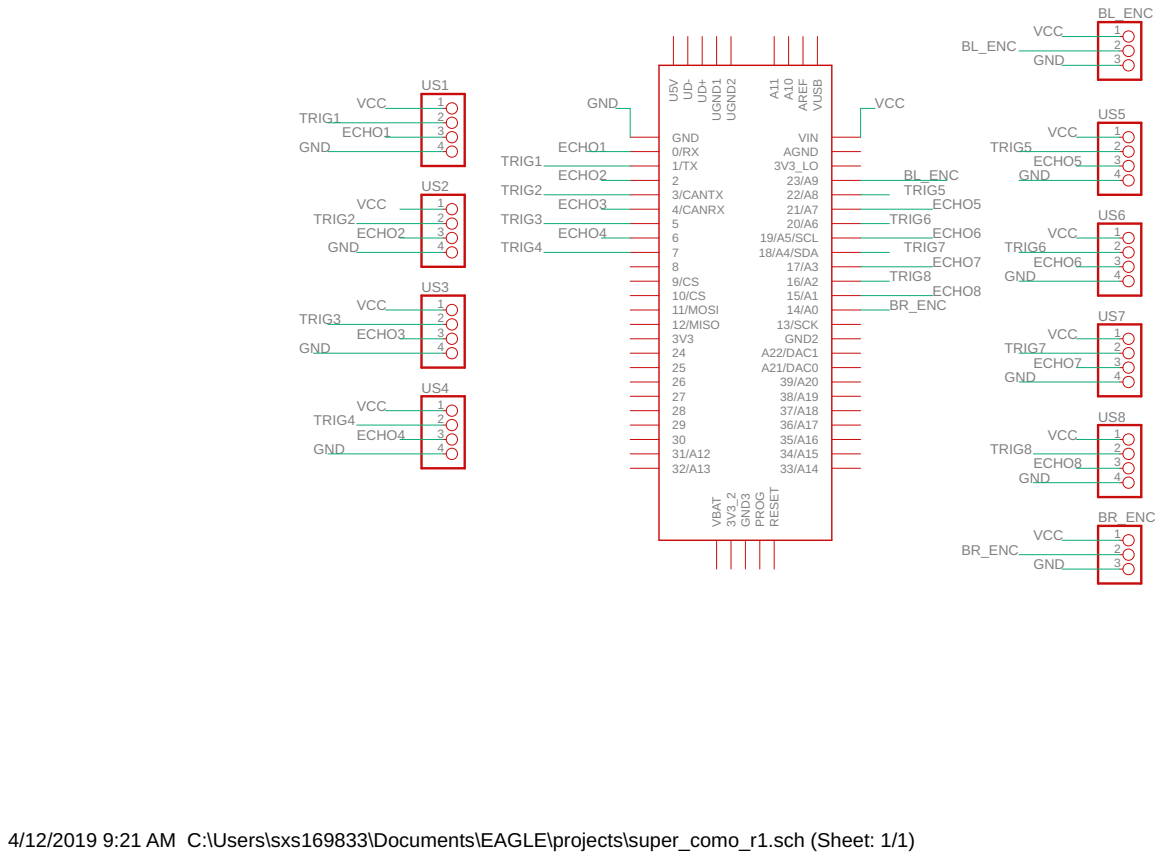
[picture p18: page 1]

4/12/2019 9:21 AM C:\Users\sxs169833\Documents\EAGLE\projects\super_como_r1.sch (Sheet: 1/1)

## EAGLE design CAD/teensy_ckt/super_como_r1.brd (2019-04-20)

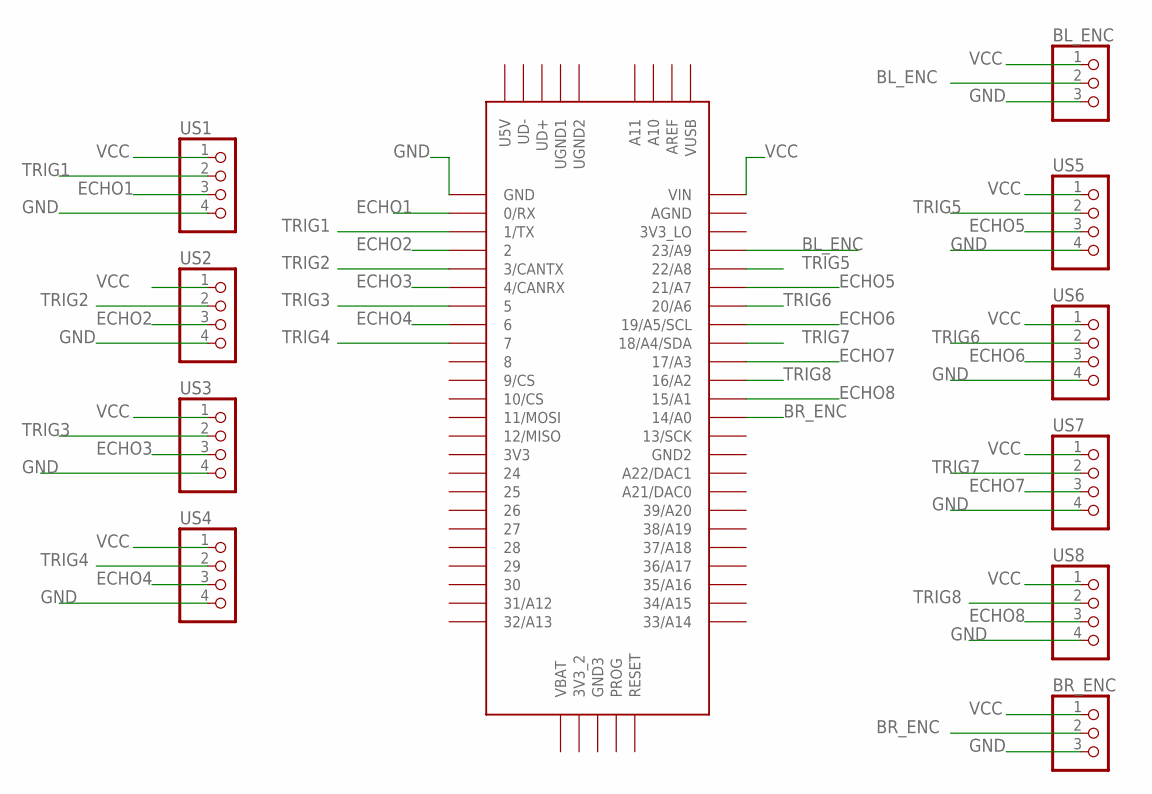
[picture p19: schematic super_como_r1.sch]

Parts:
BL_ENC: PINHD-1X3/90; 1X03/90
BR_ENC: PINHD-1X3/90; 1X03/90
U$1: TEENSY_3.5/3.6
US1, US2, US3, US4, US5, US6, US7, US8: PINHD-1X4/90; 1X04/90

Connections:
BL_ENC: BL_ENC.2, U$1.23/A9
BR_ENC: BR_ENC.2, U$1.14/A0
ECHO1: U$1.0/RX, US1.3
ECHO2: U$1.2, US2.3
ECHO3: U$1.4/CANRX, US3.3
ECHO4: U$1.6, US4.3
ECHO5: U$1.21/A7, US5.3
ECHO6: U$1.19/A5/SCL, US6.3
ECHO7: U$1.17/A3, US7.3
ECHO8: U$1.15/A1, US8.3
GND: BL_ENC.3, BR_ENC.3, U$1.GND, US1.4, US2.4, US3.4, US4.4, US5.4, US6.4, US7.4, US8.4
TRIG1: U$1.1/TX, US1.2
TRIG2: U$1.3/CANTX, US2.2
TRIG3: U$1.5, US3.2
TRIG4: U$1.7, US4.2
TRIG5: U$1.22/A8, US5.2
TRIG6: U$1.20/A6, US6.2
TRIG7: U$1.18/A4/SDA, US7.2
TRIG8: U$1.16/A2, US8.2
VCC: BL_ENC.1, BR_ENC.1, U$1.VIN, US1.1, US2.1, US3.1, US4.1, US5.1, US6.1, US7.1, US8.1

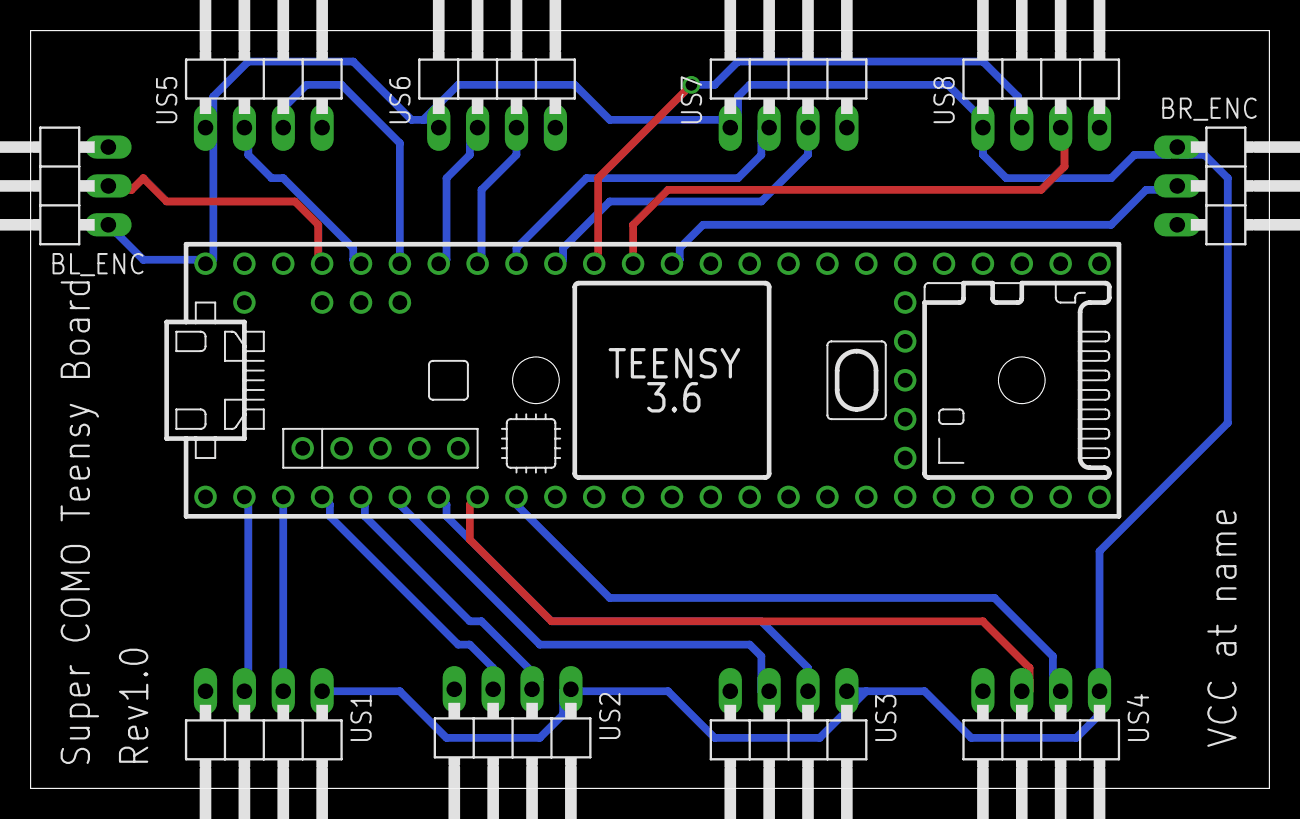
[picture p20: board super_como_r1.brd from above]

Board: 2 copper layers, 81.0 x 49.5 mm, 11 parts (0 on the bottom side), 20 nets.

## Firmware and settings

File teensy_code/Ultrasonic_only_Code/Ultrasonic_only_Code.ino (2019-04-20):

//#include <EnableInterrupt.h>

#include <ros.h>
#include <ros/time.h>
#include <hardware_interface/encoders.h>
#include <hardware_interface/ultrasonics.h>
//#include <EnableInterrupt.h>


ros::NodeHandle nh; // ROS node

// ultrasonic and encoder messages
hardware_interface::ultrasonics us;
hardware_interface::encoders enc;

// ROS publishers
ros::Publisher ultrasonicsPub("ultrasonics",&us);
ros::Publisher encodersPub("encoders", &enc);

// --------------Pins defined below--------------------------
// Front Side encoders (left to right)
// US1
int trigpin1 = 1;
int echopin1 = 0;
// US2
int trigpin2 = 3;
int echopin2 = 2;
// US3
int trigpin3 = 5;
int echopin3 = 4;
// US4
int trigpin4 = 7;
int echopin4 = 6;

// Rear Side encoders (left to right)
// US5
int trigpin5 = 22;
int echopin5 = 21;
// US6
int trigpin6 = 20;
int echopin6 = 19;
// US7
int trigpin7 = 18;
int echopin7 = 17;
// US8
int trigpin8 = 16;
int echopin8 = 15;

// Left wheel encoder
int leftencpin = 23;
// Right wheel encoder
int rightencpin = 14;
// --------------Pins defined above--------------------------


float duration1, duration2, duration3, duration4, duration5, duration6, duration7, duration8; //ultrasonic distance time measurement
float inches1, inches2, inches3, inches4, inches5, inches6, inches7, inches8; // ultrasonic distance in inches
int leftcnt, rightcnt; // encoder color change counters (each 8 are a full wheel rotation)
float leftvel, rightvel; // estimated instanteneous wheel speed
int delay1= 5; 
int delay2= 10;

//class Encoders {
//  public:
//    void 
//}
//
//void incleftcb() {
//  
//}
//
//void incrightcb() {
//  
//}


void setup()
{
  // start ROS node
  nh.initNode(); 

  // Publish topics
  nh.advertise(ultrasonicsPub); 
  nh.advertise(encodersPub);
  
  // Pin modes
  pinMode(trigpin1, OUTPUT);
  pinMode(echopin1, INPUT);
  pinMode(trigpin2, OUTPUT);
  pinMode(echopin2, INPUT);
  pinMode(trigpin3, OUTPUT);
  pinMode(echopin3, INPUT);
  pinMode(trigpin4, OUTPUT);
  pinMode(echopin4, INPUT);
  pinMode(trigpin5, OUTPUT);
  pinMode(echopin5, INPUT);
  pinMode(trigpin6, OUTPUT);
  pinMode(echopin6, INPUT);
  pinMode(trigpin7, OUTPUT);
  pinMode(echopin7, INPUT);
  pinMode(trigpin8, OUTPUT);
  pinMode(echopin8, INPUT);
  pinMode(leftencpin, INPUT_PULLUP);
  pinMode(rightencpin, INPUT_PULLUP);
  //enableInterrupt(leftencpin, incleftcb, CHANGE); // interrupt for left encoder
  //enableInterrupt(rightencpin, incrightcb, CHANGE); // interrupt for right encoder

  //Serial.begin(57600);
}
 
void loop()
{ 
  digitalWrite(trigpin1, LOW);
  delayMicroseconds(delay1);
  digitalWrite(trigpin1, HIGH);
  delayMicroseconds(delay2);
  digitalWrite(trigpin1, LOW);
  pinMode(echopin1, INPUT);
  duration1 = pulseIn(echopin1, HIGH);

  digitalWrite(trigpin2, LOW);
  delayMicroseconds(delay1);
  digitalWrite(trigpin2, HIGH);
  delayMicroseconds(delay2);
  digitalWrite(trigpin2, LOW);
  pinMode(echopin2, INPUT);
  duration2 = pulseIn(echopin2, HIGH);

  digitalWrite(trigpin3, LOW);
  delayMicroseconds(delay1);
  digitalWrite(trigpin3, HIGH);
  delayMicroseconds(delay2);
  digitalWrite(trigpin3, LOW);
  pinMode(echopin3, INPUT);
  duration3 = pulseIn(echopin3, HIGH);

  digitalWrite(trigpin4, LOW);
  delayMicroseconds(delay1);
  digitalWrite(trigpin4, HIGH);
  delayMicroseconds(delay2);
  digitalWrite(trigpin4, LOW);
  pinMode(echopin4, INPUT);
  duration4 = pulseIn(echopin4, HIGH);

  digitalWrite(trigpin5, LOW);
  delayMicroseconds(delay1);
  digitalWrite(trigpin5, HIGH);
  delayMicroseconds(delay2);
  digitalWrite(trigpin5, LOW);
  pinMode(echopin5, INPUT);
  duration5 = pulseIn(echopin5, HIGH);

  digitalWrite(trigpin6, LOW);
  delayMicroseconds(delay1);
  digitalWrite(trigpin6, HIGH);
  delayMicroseconds(delay2);
  digitalWrite(trigpin6, LOW);
  pinMode(echopin6, INPUT);
  duration6 = pulseIn(echopin6, HIGH);

  digitalWrite(trigpin7, LOW);
  delayMicroseconds(delay1);
  digitalWrite(trigpin7, HIGH);
  delayMicroseconds(delay2);
  digitalWrite(trigpin7, LOW);
  pinMode(echopin7, INPUT);
  duration7 = pulseIn(echopin7, HIGH);

  digitalWrite(trigpin8, LOW);
  delayMicroseconds(delay1);
  digitalWrite(trigpin8, HIGH);
  delayMicroseconds(delay2);
  digitalWrite(trigpin8, LOW);
  pinMode(echopin8, INPUT);
  duration8 = pulseIn(echopin8, HIGH);

  inches1 = (duration1/2)/ 74;
  inches2 = (duration2/2)/ 74;
  inches3 = (duration3/2)/ 74;
  inches4= (duration4/2)/ 74;
  inches5 = (duration5/2)/ 74;
  inches6 = (duration6/2)/ 74;
  inches7= (duration7/2)/ 74;
  inches8= (duration8/2)/ 74;

//    ultrasonic1.range = inches1;
//    ultrasonic1.radiation_type = 1;
//    ultrasonic2.range = inches2;
//    ultrasonic2.radiation_type = 2;
//    ultrasonic3.range = inches3;
//    ultrasonic3.radiation_type = 3;
//    ultrasonic4.range = inches4;
//    ultrasonic4.radiation_type = 4;
//    ultrasonic5.range = inches5;
//    ultrasonic5.radiation_type = 5;
//    ultrasonic6.range = inches6;
//    ultrasonic6.radiation_type = 6;
//    ultrasonic7.range = inches7;
//    ultrasonic7.radiation_type = 7;
//    ultrasonic8.range = inches8;
//    ultrasonic8.radiation_type = 8;


    us.us1 = inches1/39.37; //divide by 39.37 to convert to metric scale
    us.us2 = inches2/39.37;
    us.us3 = inches3/39.37;
    us.us4 = inches4/39.37;
    us.us5 = inches5/39.37;
    us.us6 = inches6/39.37;
    us.us7 = inches7/39.37;
    us.us8 = inches8/39.37;
    us.timestamp = nh.now();
    
//    chatter1.publish(&ultrasonic1);
//    chatter2.publish(&ultrasonic2);
//    chatter3.publish(&ultrasonic3);
//    chatter4.publish(&ultrasonic4);
//    chatter5.publish(&ultrasonic5);
//    chatter6.publish(&ultrasonic6);
//    chatter7.publish(&ultrasonic7);
//    chatter8.publish(&ultrasonic8);
   ultrasonicsPub.publish(&us);
    

  nh.spinOnce();
  /*
  unsigned long time;
  time = millis()/1000;
  Serial.print(time);
  Serial.print(": ");
  Serial.print(inches1);
  Serial.print("in 1, ");
  Serial.print(inches2);
  Serial.print("in 2, ");
  Serial.print(inches3);
  Serial.print("in 3, ");
  Serial.print(inches4);
  Serial.print("in 4, ");
  Serial.print(inches5);
  Serial.print("in 5, ");
  Serial.print(inches6);
  Serial.print("in 6, ");
  Serial.print(inches7);
  Serial.print("in 7, ");
  Serial.print(inches8);
  Serial.print("in 8, ");
  Serial.println();
  */
  delay(60);
}

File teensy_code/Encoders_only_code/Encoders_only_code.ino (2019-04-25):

#include <ros.h>
//#include <ros.h>
#include <ros/time.h>
#include <hardware_interface/encoders.h>
//#include </home/nvidia/arduino-1.8.7/hardware/tools/avr/avr/include/avr/interrupt.h>

#include </home/nvidia/arduino-1.8.7/hardware/teensy/avr/cores/teensy3/avr/interrupt.h>
//#include <EnableInterrupt.h>

const int ENC_BL_PIN = 23;
const int ENC_BR_PIN = 14;
volatile uint8_t updateFlagsShared;
uint8_t updateFlags;
const int BL_FLAG = 1;
const int BR_FLAG = 2;

    volatile int BL_count_shared = 0;
    volatile int BR_count_shared = 0;
    int BL_count = 0;
    int BR_count = 0;
    int BL_count_old = 0;
    int BR_count_old = 0;
    float vel_BL = 0;
    float vel_BR = 0;
    
    volatile unsigned long BL_new_time = 0;
    volatile unsigned long BR_new_time = 0;
    volatile unsigned long BL_old_time = 0;
    volatile unsigned long BR_old_time = 0;
    unsigned long BL_DeltaTime = 0;
    unsigned long BR_DeltaTime = 0;
    
float pi  = 3.141593;
float R   = 0.051; 
volatile unsigned long dt;
volatile unsigned long t0;

hardware_interface::encoders enc;
hardware_interface::encoders enc_vel;

ros::NodeHandle nh;
ros::Publisher pub_encoder("encoders_count", &enc);
ros::Publisher pub_vel_est("encoders_vel", &enc_vel);

void incBL() {
  BL_count_shared++;
  BL_old_time = BL_new_time;
  BL_new_time = micros();
  updateFlagsShared |= BL_FLAG;
}

void incBR() {
  BR_count_shared++;
  BR_old_time = BR_new_time;
  BR_new_time = micros();
  updateFlagsShared |= BR_FLAG;
}

void readAndCopyInputs() {
  if (updateFlagsShared) {
    // Turn off interrupts, make local copies of variables set by interrupts,
    // then turn interrupts back on. Without doing this, an interrupt could
    // update a shared multibyte variable while the loop is in the middle of
    // reading it
    //noInterrupts();
    // make local copies
    updateFlags = updateFlagsShared;
    if(updateFlags & BL_FLAG) {
      BL_count = BL_count_shared;
      BL_DeltaTime = BL_new_time - BL_old_time;
    }
    if(updateFlags & BR_FLAG) {
      BR_count = BR_count_shared;
      BR_DeltaTime = BR_new_time - BR_old_time;
    }
    // clear shared update flags and turn interrupts back on
    updateFlagsShared = 0;
    //interrupts();
  }
}

void calcVelocityEstimate() {
    if(BL_count_old != BL_count){
        vel_BL = 0.25*pi*R/(BL_DeltaTime/1000000.0);    }
    else{ vel_BL = 0.0; }

    if(BR_count_old != BR_count){
        vel_BR = 0.25*pi*R/(BR_DeltaTime/1000000.0);    }
    else{ vel_BR = 0.0; }

    // update history
    BL_count_old = BL_count;
    BR_count_old = BR_count;
}

void setup() {
  nh.initNode();
  pinMode(ENC_BR_PIN, INPUT_PULLUP);
  pinMode(ENC_BL_PIN, INPUT_PULLUP);
  attachInterrupt(digitalPinToInterrupt(ENC_BR_PIN), incBR, CHANGE);
  attachInterrupt(digitalPinToInterrupt(ENC_BL_PIN), incBL, CHANGE);
  nh.advertise(pub_encoder);
  nh.advertise(pub_vel_est);
  t0 = millis();
}

void loop() {
  dt = millis() - t0;
if (dt > 50) {
    readAndCopyInputs();

    // publish velocity estimate
    calcVelocityEstimate();
    //vel_est.BL  = car.getVelEstBL();
    //vel_est.BR  = car.getVelEstBR();
    //pub_vel_est.publish(&vel_est); 

    // publish encoder ticks
    enc.BL = BL_count;
    enc.BR = BR_count;
    enc.timestamp = nh.now();
    pub_encoder.publish(&enc);

    // publish encoder estimated vel
    enc_vel.BL = vel_BL;
    enc_vel.BR = vel_BR;
    enc_vel.timestamp = nh.now();
    pub_vel_est.publish(&enc_vel);

    t0 = millis();
  }
  nh.spinOnce();
}

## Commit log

2018-11-08 adding lidar and imu packages + modifications
    [URG.cfg, ZED.stl, ZEDM.stl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]
2018-11-08 returning submodules
    [URG.cfg, ZED.stl, ZEDM.stl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]
2019-02-06 Adding script to set up (USB) device rules
2019-04-20 Adding CAD files
    adding some teensy arduino code too and editing readme files
    [Ultraschallsensorhalterung_4.stl, deck1.SLDPRT, deck2.SLDPRT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]
2019-04-25 updating teensy code + launch files
2019-05-01 adding bill of materials
    [super_como_parts_list.xlsx]
